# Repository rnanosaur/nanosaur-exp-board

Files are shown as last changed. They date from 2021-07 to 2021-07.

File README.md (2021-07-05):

# :sauropod: nanosaur expansion board - [][cc-by-nc-sa]


NanoSaur is a little tracked robot ROS2 enabled, made for an NVIDIA Jetson Nano

* Website: [nanosaur.ai](https://nanosaur.ai)
* Do you need an help? [Discord](https://discord.gg/NSrC52P5mw)
* For technical details follow [wiki](https://github.com/rnanosaur/nanosaur/wiki)
* Something wrong? Open an [issue](https://github.com/rnanosaur/nanosaur/issues)

# How make Nanosaur PCBs on PCBWay

- Register to PCBWay using [my refferer link](https://www.pcbway.com/setinvite.aspx?inviteid=472567)
- Upon you registered, go to the <a href="https://www.pcbway.com/project/shareproject/Nanosaur___The_smallest_NVIDIA_Jetson_dinosaur_robot.html">nanosaur PCB from PCBWay</a>
- Click on **"Add to Cart"** button on the right
- A pop-up will show up: all default settings are good. You must only select how many PCBs you want: the minimum quantity, by default, is 5. The first order of 5 PCBs is free on PCBWay: you must pay only the shipping costs

# Board design

This board is a simple adapter to connect the motor controller and the LCDs to the NVIDIA Jetson on your NanoSaur, this board connect:

* I2C bus 0 (Pin 27, 28)
  * oled right
* I2C bus 1 (Pin 3, 5)
  * oled left
  * adafruit motor control
* 2 custom buttons
  * GPIO Pin 31
  * GPIO Pin 33

## NVIDIA Jetson Reference

* Jetsonhacks [Jetson Nano pinout](https://www.jetsonhacks.com/nvidia-jetson-nano-j41-header-pinout/)

## Expansion board reference

Watch the documentation on [nanosaur expansion board](https://nanosaur.ai/expansion-board/)

Schematic expansion board

### PCB

Layout PCB

PCB Top expansion board

PCB Bottom expansion board

# Develop

The documentation is made using [Kicad](https://www.kicad.org/) 5

The CI is made using
* [Kibot](https://github.com/INTI-CMNB/KiBot)
* [kicad-exports](https://github.com/nerdyscout/kicad-exports)

# License

This project is under license [Creative Commons Attribution-NonCommercial-ShareAlike 4.0 International License][cc-by-nc-sa].

[cc-by-nc-sa]: http://creativecommons.org/licenses/by-nc-sa/4.0/
[cc-by-nc-sa-image]: https://licensebuttons.net/l/by-nc-sa/4.0/88x31.png
[cc-by-nc-sa-shield]: https://img.shields.io/badge/License-CC%20BY--NC--SA%204.0-lightgrey.svg

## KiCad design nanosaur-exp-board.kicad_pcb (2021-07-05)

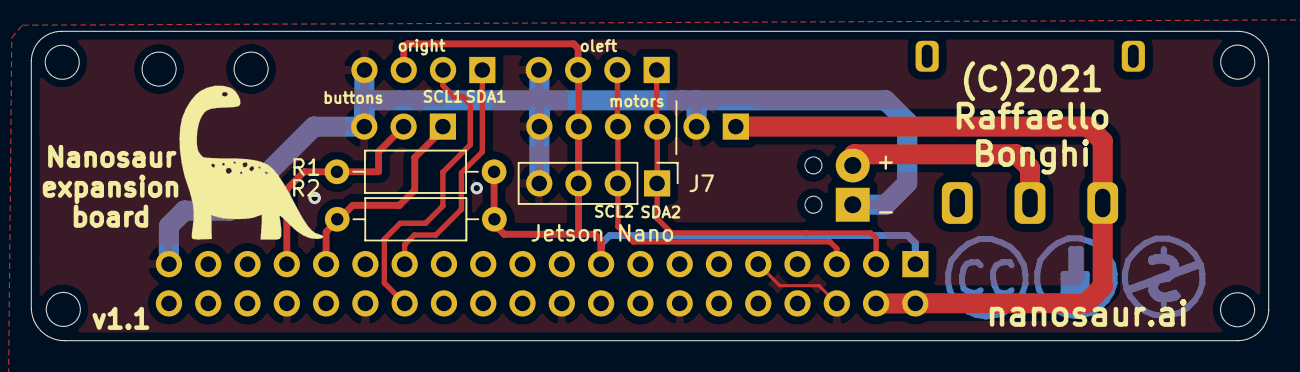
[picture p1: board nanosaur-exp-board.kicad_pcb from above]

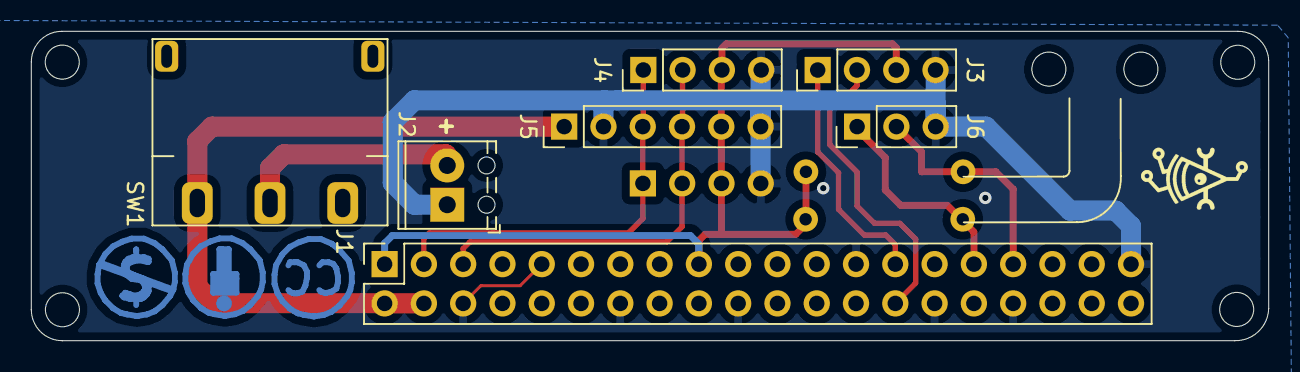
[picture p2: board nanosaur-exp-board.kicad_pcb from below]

Board: 2 copper layers, 80.0 x 20.0 mm, 16 parts (7 on the bottom side), 10 nets.

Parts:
H1, H2, H3, H4, H5, H6: MountingHole; MountingHole_2.2mm_M2
J1: jetson_nano; PinSocket_2x20_P2.54mm_Vertical
J2: Screw_Terminal_01x02; TerminalBlock_Phoenix_MPT-0,5-2-2.54_1x02_P2.54mm_Horizontal
J3, J4: Conn_i2c_oled; PinHeader_1x04_P2.54mm_Vertical
J5: Conn_motors; PinHeader_1x06_P2.54mm_Vertical
J6: Conn_buttons; PinHeader_1x03_P2.54mm_Vertical
J7: Conn_01x04; PinHeader_1x04_P2.54mm_Vertical
R1, R2: 1k; R_Axial_DIN0207_L6.3mm_D2.5mm_P10.16mm_Horizontal
SW1: SW_SPDT; slide_switch_4.7mm

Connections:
+3V3: J1.1, J1.17, J3.3, J4.3, J5.5, J7.3, R1.1, R2.1
GND: J1.6, J1.9, J1.14, J1.20, J1.25, J1.30, J1.34, J1.39, J2.1, J3.4, J4.4, J5.2, J5.6, J6.3, J7.4
unnamed: J1.3, J4.1, J5.3, J7.1
unnamed: J1.5, J4.2, J5.4, J7.2
unnamed: J1.27, J3.1
unnamed: J1.28, J3.2
unnamed: J1.31, J6.1, R2.2
unnamed: J1.33, J6.2, R1.2
unnamed: J2.2, SW1.2
VCC: J1.2, J1.4, J5.1, SW1.1

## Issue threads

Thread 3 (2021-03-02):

Complete schematics and PCB design

rbonghi, 2021-03-02:
Complete the schematics and PCB design
https://github.com/rnanosaur/nanosaur-exp-board/issues/2

Closed 2021-05-09.

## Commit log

2021-02-26 Fix layout board
    [nanosaur-exp-board.kicad_pcb, nanosaur-exp-board.sch]
2021-02-26 Exp improvements
    [nanosaur-exp-board.kicad_pcb, nanosaur-exp-board.sch]
2021-02-27 Test actions
    [nanosaur-exp-board.sch]
2021-02-28 Chanfe from kibot action to kicad-exports
2021-02-28 New workflow test
    [nanosaur-exp-board.kicad_pcb]
2021-03-01 fix pcbdraw
2021-05-05 improve expansion board and fix schematic
    [nanosaur-exp-board.kicad_pcb, nanosaur-exp-board.sch]
2021-05-05 minor fixes
    [nanosaur-exp-board.kicad_pcb, nanosaur-exp-board.sch]
2021-05-08 Add gerber
2021-05-08 test footprint libraries
2021-05-08 Improve sch and pcb
    [nanosaur-exp-board.kicad_pcb, nanosaur-exp-board.sch]
2021-05-08 Improve pcb
    [nanosaur-exp-board.kicad_pcb, nanosaur-exp-board.sch]
2021-05-09 Improve sch and azz gerber zip
    [nanosaur-exp-board.kicad_pcb, nanosaur-exp-board.sch]
2021-05-09 Fix CI
    [nanosaur-exp-board.sch]
2021-05-09 Test gerber zip
2021-05-09 Improve gerber
2021-05-09 Fix kibot and pcb
    [nanosaur-exp-board.kicad_pcb]
2021-05-10 Improve PCB layout, fix BOM, improve sch
    [nanosaur-exp-board.kicad_pcb, nanosaur-exp-board.sch]
2021-05-10 Final PCB fix
    [nanosaur-exp-board.kicad_pcb]
2021-05-10 fix bom
    [nanosaur-exp-board.sch]
2021-06-08 Fix license and minor fixes
    [nanosaur-exp-board.kicad_pcb]
2021-07-05 Fix readme
    [nanosaur-exp-board.kicad_pcb, nanosaur-exp-board.sch]
2021-07-05 Fix DRC
    [nanosaur-exp-board.kicad_pcb]
2021-07-07 Bump nerdyscout/kicad-exports from 2.2 to 2.3
    Bumps [nerdyscout/kicad-exports](https://github.com/nerdyscout/kicad-exports) from 2.2 to 2.3.
    - [Release notes](https://github.com/nerdyscout/kicad-exports/releases)
    - [Changelog](https://github.com/nerdyscout/kicad-exports/blob/main/CHANGELOG.md)
    - [Commits](https://github.com/nerdyscout/kicad-exports/compare/v2.2...v2.3)
    ---
    updated-dependencies:
    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
2021-12-27 Reference buy url
    [nanosaur-exp-board.sch]
2021-12-29 Added other documentation fields
    [nanosaur-exp-board.sch]
2021-12-29 fix table fields
    [nanosaur-exp-board.sch]
2021-12-29 Fix gerber zip build

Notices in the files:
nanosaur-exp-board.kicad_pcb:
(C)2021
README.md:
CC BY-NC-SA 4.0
